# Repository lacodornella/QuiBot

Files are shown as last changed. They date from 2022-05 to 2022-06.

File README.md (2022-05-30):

# QuiBot

QuiBot is a robot to experiment basic sequential programming for children. No computer is needed as it can be programmed by using painted wooden blocks, where each color represents a different action. The robot has a backpack that can contain up to 12 blocks that execute as soon as they're consumed.

QuiBot Image

## Project folders

The project uses the following folders:
 - [3D Design](./3D_design/): 3D assembly process, BOM and printing files
 - [ESP-32 Arduino program](./QuiBot/): C++ Arduino program
 - [Kicad PCB project](./PCB_QuiBot/): Kicad PCB project
 - [Images](./Images/): Used to store some project images

## Development

This robot has been conceived and developed by Aleix Badia and [Pau Lafoz](https://www.github.com/pau-lafoz) from La Codornella under the UPC project "Qui-Bot H2O", led by Marta Tarrés and Toni Dorado, and funded by FECYT.

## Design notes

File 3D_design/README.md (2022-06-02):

# 3D Design

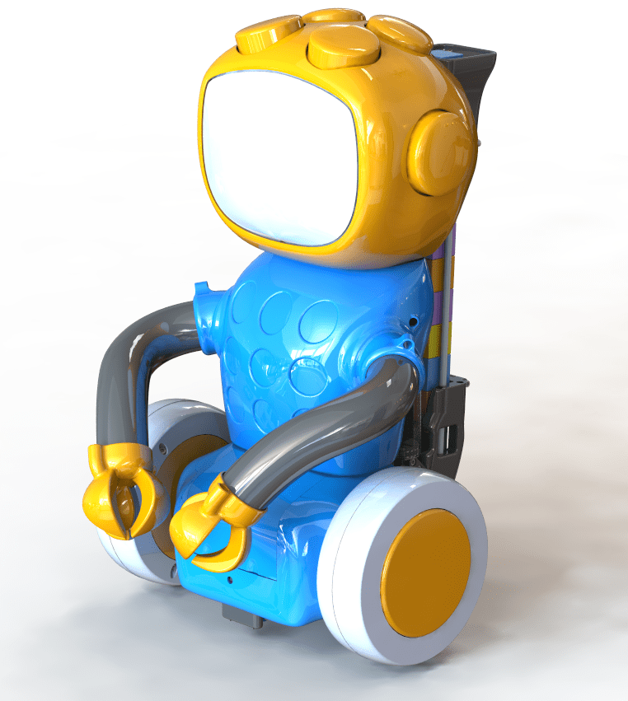
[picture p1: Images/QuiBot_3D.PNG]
QuiBot 3D


## Printing process
The list and details of all printable parts in the project can be found on [3D_Parts_list](./3D_parts_list.pdf) file.

Other considerations:
 - 5 printing configurations are used in the project.
 - All the printings can be done with standard 20 cm cube volume FDM printer.
 - The printing positions are shown in the folder "3D printing positioning captions". 

## Bill of materials
Detailed on the [BOM](./BOM.pdf) and [BOM Screws](./BOM_Screws.pdf) files. 

## Assembly process
The assembly process can be done using the schematic [QuiBot_drawings.pdf](./QuiBot_drawings.PDF) and opening the [Qui-bot.FCStd](./Qui-bot.FCStd) document with FreeCad for further details. 

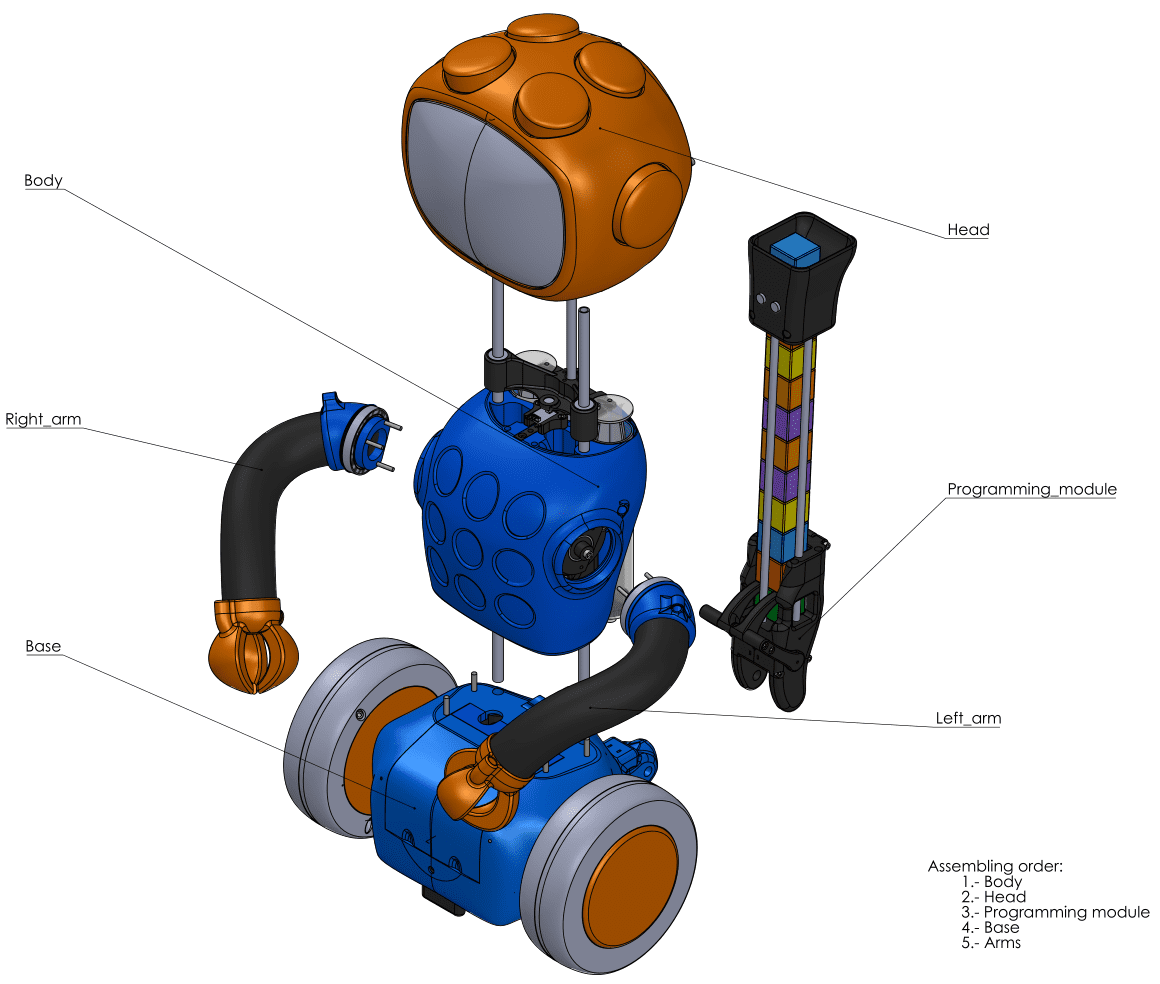
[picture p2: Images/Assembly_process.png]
Assembly process


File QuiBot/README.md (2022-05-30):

# QuiBot Arduino program

## Installation

The ESP32 controller can be programmed using Arduino IDE. The following libraries are required:
 - [FastLed](https://github.com/FastLED/FastLED)
 - [Adafruit_VL53L0X](https://github.com/adafruit/Adafruit_VL53L0X)
 - [TCS34725](https://github.com/hideakitai/TCS34725)
 - [AccelStepper](https://github.com/waspinator/AccelStepper)

 ## Hardware

The controller used is an ESP32 that controls the following devices:
 - Motion:
    - Wheels: 2x NEMA 17 Steppers with planetary reductor
    - Arms: 2x NEMA 17 Steppers with timing belt reduction
    - Syringe: NEMA 17 Stepper with endless screw
    - Block ejection: 5V Servomotor
 - Sensors:
    - Color sensor: TCS34725
    - Laser distance sensor: VL53L0X
    - Line follower: 2x TCRT5000
    - Arm endstops: 2x Hall effect sensor
    - Syringe endstop: Hall effect sensor
 - Eyes:
    - 2x 8x8 Adressable RGB Led matrix

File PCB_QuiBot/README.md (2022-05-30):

# QuiBot Kicad Project

## 3D View
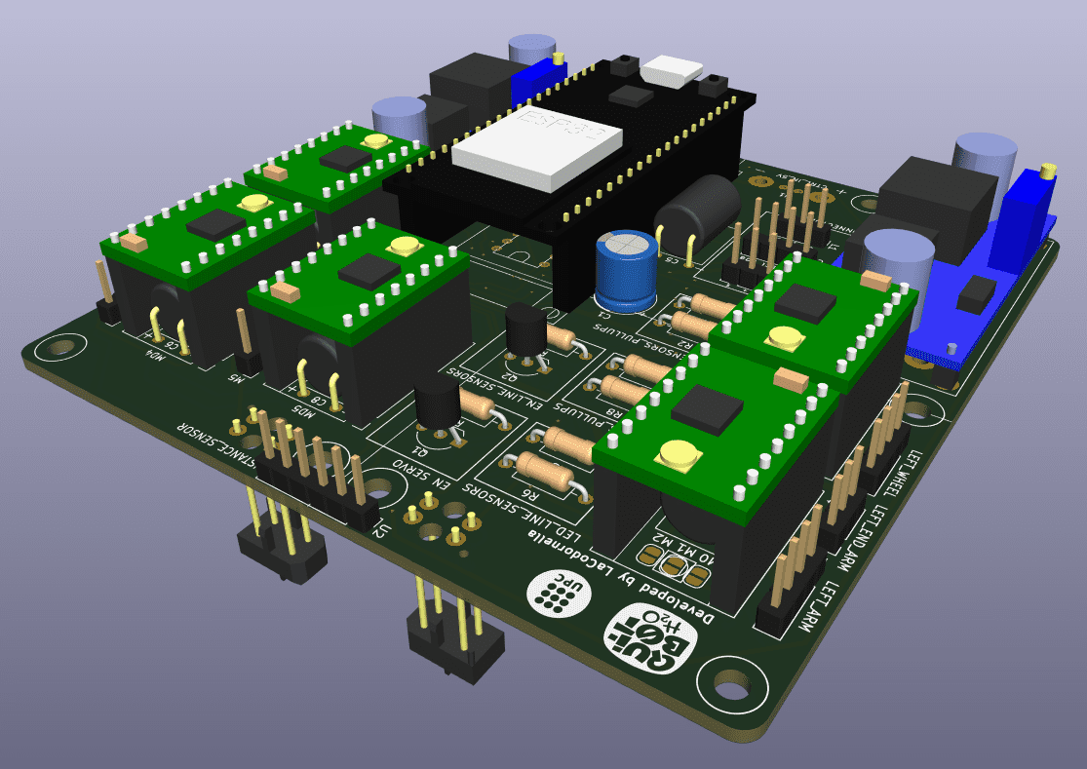
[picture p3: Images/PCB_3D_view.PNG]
PCB QuiBot 3D view


## Layout
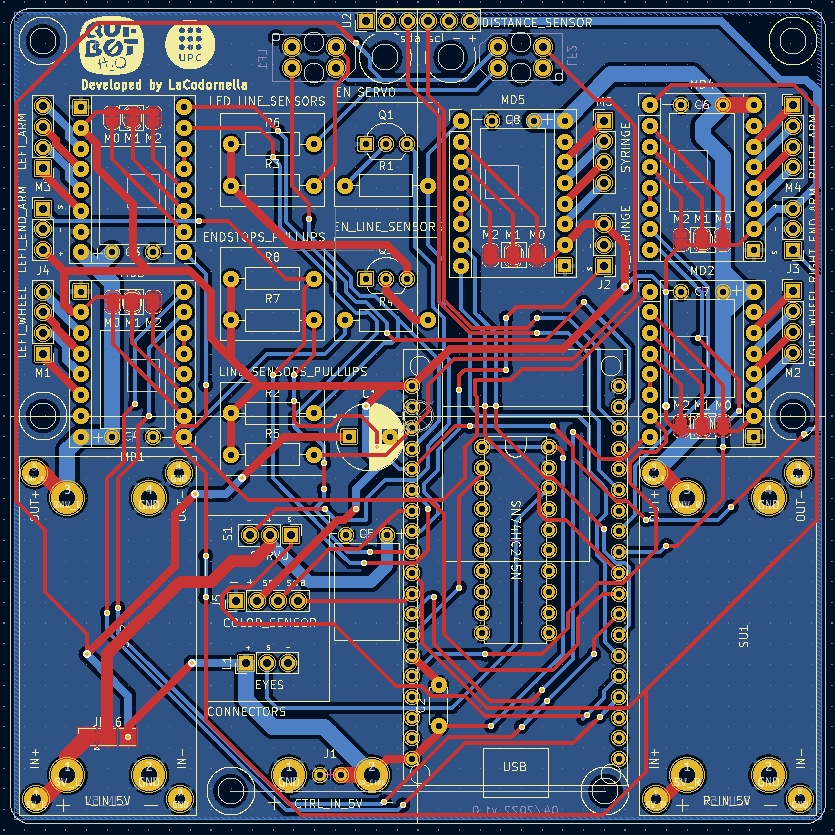
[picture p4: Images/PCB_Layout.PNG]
PCB QuiBot Layout


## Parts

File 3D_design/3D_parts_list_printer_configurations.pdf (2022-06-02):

| | QuiBot_1 | QuiBot_2 | QuiBot_3 | QuiBot_4 | QuiBot_5
Quality | Layer Height | 0.2 | 0.2 | 0.15 | 0.2 | 0.15
| Initial Layer Height | 0.15 | 0.15 | 0.15 | 0.15 | 0.15
Walls | Wall thikness | 0.8 | 0.8 | 0.8 | 2.0 | 2.0
Top/Bottom | Top/bottom pattern | Lines | Lines | Lines | Lines | Lines
| Bottom pattern initial layer | Concentric | Lines | Lines | Lines | Lines
Infill | Infill density | 10% | 25% | 15% | 15% | 40%
Material | Printing temperature | 200ºC | 200ºC | 200ºC | 200ºC | 200ºC
| Speed | 60 mm/s | 40 mm/s | 50 mm/s | 50 mm/s | 50 mm/s
Support | Generate support
| Support Overhang Angle | | 84º | 84º | 84º | 84º

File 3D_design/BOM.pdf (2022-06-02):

Module | Name in design | Component | Utilitzation | Price | Percent total price Shop | Comments | Link

Moviment

Nema17_5.18_reduction | Stepper amb reductor R | Moviment de la roda dreta del robot | 45,46 € | 10,82% | AliExpress | Compra pak de 4 a través d'aliexpress | https://es.aliexpress.com/item/4000222067282.html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
Nema17_5.18_reduction | Stepper amb reductor L | Moviment de la roda esquerra del robot | 45,46 € | 10,82% | AliExpress | Compra pak de 4 a través d'aliexpress | https://es.aliexpress.com/item/4000222067282.html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
Pololu_A4988 | Controlador A4988 DRV8825 | Controlador roda dreta | 2,20 € | 0,52% | Amazon | Compra pack de 5 a Amazon | https://www.amazon.es/UKCOCO-Reprap-Stepper-disipador-impresora/dp/B07BMR39GQ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
Pololu_A4988 | Controlador A4988 DRV8825 | Controlador roda esquerra | 2,20 € | 0,52% | Amazon | Compra pack de 5 a Amazon | https://www.amazon.es/UKCOCO-Reprap-Stepper-disipador-impresora/dp/B07BMR39GQ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
TCRT_5000_Line_follower | Sensor detector de línia dret | Detecció de la línia dreta | 0,49 € | 0,12% | Amazon | Compra pack de 10 a Amazon | https://www.amazon.es/gp/product/B08CSRNCMG/ref=ox_sc_act_title_1?smid=A1A94E00UJ9A5S&psc=1
TCRT_5000_Line_follower | Sensor detector de línia esquerra | Detecció de la línia esquerra | 0,49 € | 0,12% | Amazon | Tub de 5 a RS | https://www.amazon.es/gp/product/B08CSRNCMG/ref=ox_sc_act_title_1?smid=A1A94E00UJ9A5S&psc=1
CJVL53LOXV2_IR_distanse_sensor Sensor de distància GY-VL53L0XV2 | Detecció del pot de plàstic | 4,75 € | 1,13% | Amazon | Compra pack de 3 a Amazon | https://www.amazon.es/Haudboin-VL53L0X-Sensor-distancia-GY-VL53L0XV2/dp/B09QCJM193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
DC-DC_XL6009E1 | Step up | Elevació 5V poqer bank a 12V pels steppers | 2,41 € | 0,57% | Amazon | Compra pack de 5 a Amazon | https://www.amazon.es/TECNOIOT-XL6009-Booster-Adjustable-Step-up/dp/B07HB3GMZD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

Braços

Syringe | 2 Xeringues amb tub | Xeringues per xuclar el líquid | 11,15 € | 2,66% | Amazon | Compra pack de 2 a Amazon | https://www.amazon.es/dp/B081RL7BMH/?coliid=I3OZAKCWK8IAB6&colid=2GDHV7MAEUG1F&psc=1&ref_=lv_ov_lig_dp_it
Worm_gear_bar | Barra roscada lineal | Actuador per moure l'èmbol de les xeringues | 6,19 € | 1,47% | Amazon | Compra individual a Amazon | https://www.amazon.es/SIENOC-Impresora-Varilla-Carril-lineal/dp/B07LDZY8RY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
Nema17 | Stepper nema 17 Xeringa | Motor xeringa | 7,07 € | 1,68% | Amazon | Compra pack de 3 a Amazon | https://www.amazon.es/dp/B092ZD2WMV/ref=twister_B09BZHBBB5?_encoding=UTF8&psc=1
Nema17 | Stepper nema 17 R | Motor del braç dret | 7,07 € | 1,68% | Amazon | Compra pack de 3 a Amazon | https://www.amazon.es/dp/B092ZD2WMV/ref=twister_B09BZHBBB5?_encoding=UTF8&psc=1
Nema17 | Stepper nema 17 L | Motor del braç esquerra | 7,07 € | 1,68% | Amazon | Compra pack de 3 a Amazon | https://www.amazon.es/dp/B092ZD2WMV/ref=twister_B09BZHBBB5?_encoding=UTF8&psc=1
Pololu_A4988 | Controlador A4988 DRV8825 | Controlador braç dret | 2,20 € | 0,52% | Amazon | Compra pack de 5 a Amazon | https://www.amazon.es/UKCOCO-Reprap-Stepper-disipador-impresora/dp/B07BMR39GQ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
Pololu_A4988 | Controlador A4988 DRV8825 | Controlador braç esquerra | 2,20 € | 0,52% | Amazon | Compra pack de 5 a Amazon | https://www.amazon.es/UKCOCO-Reprap-Stepper-disipador-impresora/dp/B07BMR39GQ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
Pololu_A4988 | Controlador A4988 DRV8825 | Controlador motor xeringa | 2,20 € | 0,52% | Amazon | Compra pack de 5 a Amazon | https://www.amazon.es/UKCOCO-Reprap-Stepper-disipador-impresora/dp/B07BMR39GQ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
Hall_sensor | Fi de cursa dels braços | Detectar el final del moviment de cada un dels braços | 3,71 € | 0,88% | Amazon | Compra pack de 6 a Amazon | https://www.amazon.es/GTIWUNG-interruptor-Interruptor-Compatible-Impresora/dp/B07VWRS24K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
DC-DC_XL6009E1 | Step up | Elevació 5V power bank a 12V pels steppers | 4,81 € | 1,15% | Amazon | Compra pack de 5 a Amazon | https://www.amazon.es/TECNOIOT-XL6009-Booster-Adjustable-Step-up/dp/B07HB3GMZD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
| Corretges 200 mm reducció braços | Reduir el parell necessari per aixecar els braços guanyant precissió a la punta | 2,18 € | 0,52% | Amazon | Compra pack de 10 a Amazon | https://www.amazon.es/3Dman-GT2-distribuci%C3%B3n-impresora-unidades/dp/B07V6N32B1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
Bearing_52_40_7 | 2 x Rodaments 6808ZZ - 40 mm x 52 mm x 7 mm | Guiar exteriorment el moviments dels braços | 11,09 € | 2,64% | Amazon | Compra pack de 4 a Amazon | https://www.amazon.es/gp/product/B081JT8WJY/ref=ppx_yo_dt_b_asin_title_o06_s00?ie=UTF8&psc=1
608_2RS bearing | 4 x Rodaments 604-609 WX2RS | Guiar interiorment el moviments dels braços | 6,62 € | 1,58% | Amazon | Compra pack de 10 a Amazon | https://www.amazon.es/gp/product/B07JJ526NX/ref=ppx_yo_dt_b_asin_title_o00_s00?ie=UTF8&th=1
Lineal_bearing | 2 x Rodaments lineals de 8mm de diàmetre interior Guiar el moviment de les xeringues | 1,38 € | 0,33% | Amazon | Compra pack de 12 a Amazon | https://www.amazon.es/QWORK-LM8UU-Rodamientos-lineales-impresora/dp/B086W1LMMZ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
8x2.5_Magnet | 9 x Imants de neodimi N52. Discs de 8x3 mm | Finals de cursa dels braços, les xeringues i unió del bloc programador | 3,57 € | 0,85% | Amazon | Compra pack de 25 a Amazon | https://www.amazon.es/gp/product/B00Z7YVU8A/ref=ppx_yo_dt_b_search_asin_title?ie=UTF8&psc=1
| 2 x molles 35mm x 7mm x 0,5mm | Contrapes braços. | 0,09 € | 0,02% | Amazon | Compra pack a Amazon | https://www.amazon.es/gp/product/B01KG024CU/ref=ppx_yo_dt_b_search_asin_title?ie=UTF8&psc=1

Estètica

8x8_LED_matrix | Matriu LED 8x8 ull dret | matrius LED per fer d'ull dret | 17,26 € | 4,11% | Amazon | Compra individual a Amazon | https://www.amazon.es/BTF-LIGHTING-0-24ft0-24ft-Programmed-Individually-Addressable/dp/B01DC0IMRW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
8x8_LED_matrix | Matriu LED 8x8 ull esquerra | matrius LED per fer d'ull esquerra | 17,26 € | 4,11% | Amazon | Compra individual a Amazon | https://www.amazon.es/BTF-LIGHTING-0-24ft0-24ft-Programmed-Individually-Addressable/dp/B01DC0IMRW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

Bloc
programador
TCS34725_RGB_sensor | TCS34725 RGB Color Sensor | Llegir el color dels blocs de fusta | 4,42 € | 1,05% | Amazon | Compra pack de 5 a Amazon | https://www.amazon.es/dp/B07YXDZVJN/?coliid=IXUG4P6WHKAOW&colid=2GDHV7MAEUG1F&psc=1&ref_=lv_ov_lig_dp_it
SG90 - Micro Servo 9g | Servo Motor SG90 | Expulsar els blocs un cop llegits | 2,64 € | 0,63% | Amazon | Compra pack de 5 a Amazon | https://www.amazon.es/Micro-Helicopter-Airplane-Controls-LKY66-UK-5/dp/B07236KYVC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

Controlador

ESP32_DEVKIT_AZD | ESP32 | Microcontrolador | 6,61 € | 1,57% | Amazon | Compra pack de 5 a Amazon | https://www.amazon.es/AZDelivery-NodeMCU-ESP-WROOM-32-Tablero-Desarrollo/dp/B074RG86SR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
Power_bank | Power bank 10000 mAh LEFT | Power bank 10000 mAh costat dret | 12,63 € | 3,01% | Amazon | Compra individual a Amazon | https://www.amazon.es/BABAKA-10000mAh-Cargador-Port%C3%A1til-Tecnolog%C3%ADa/dp/B08H89HP33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
Power_bank | Power bank 10000 mAh RIGHT | Power bank 10000 mAh costat esquerre | 12,63 € | 3,01% | Amazon | Compra individual a Amazon | https://www.amazon.es/BABAKA-10000mAh-Cargador-Port%C3%A1til-Tecnolog%C3%ADa/dp/B08H89HP33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
Power_bank | Power bank 10000 mAh controlador i resta | Power bank 10000 mAh controlador i resta | 12,63 € | 3,01% | Amazon | Compra individual a Amazon | https://www.amazon.es/BABAKA-10000mAh-Cargador-Port%C3%A1til-Tecnolog%C3%ADa/dp/B08H89HP33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
PCB_QuiBot | PCB | | 25,00 € | 5,95% | Fabricació a ELECROW
| Electrònica soldada a la PCB | | 15,00 € | 3,57% | Botiga genèrica d'electrònica

Altres

Strucutural_vertical_bar | materials constructius (fusta i tubs alumini) | | 40,00 € | 9,52% | Fes més bricolatge
| Impressió 3D | 2,1 Kg de plàstic contats a 20€ el Kg | 41,86 € | 9,97% | | | https://www.amazon.es/gp/product/B08LSF322C/ref=ppx_yo_dt_b_asin_title_o08_s00?ie=UTF8&th=1
| Cargoleria *Detallat al full cargoleria | | 30,00 € | 7,14% | Botiga genèrica de cargoleria
Total: | 419,96 €

Opcionals

Lona decorat | 60,00 € | https://www.ecoimpresion.es/lonas/pvc.html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
Pots de plàstic | 20,00 €
Total: | 80,00 €
Total + opcionals: | 499,96 €

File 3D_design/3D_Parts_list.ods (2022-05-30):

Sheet: 3D printed parts
 |  | 252:25:00 | 2093
 | Name | Printing time | Plastic (g) | Material | Configuration
1 | Arms_motors_support_bottom | 2:49:00 | 24 | PLA negre | QuiBot_2
1 | Arms_motors_support_top | 3:11:00 | 27 | PLA negre | QuiBot_2
1 | Ball_support | 2:13:00 | 18 | PLA blau | QuiBot_3
1 | Ball_support_inferior | 0:23:00 | 3 | PLA blau | QuiBot_3
1 | Batteries_lid | 3:15:00 | 29 | PLA blau | QuiBot_3
1 | Batteries_support | 8:03:00 | 82 | PLA negre | QuiBot_4
1 | Big_pulley | 2:17:00 | 21 | PLA negre | QuiBot_2
1 | Big_pulley_mirror | 2:17:00 | 21 | PLA negre | QuiBot_2
1 | Block_insert | 5:35:00 | 42 | PLA negre | QuiBot_3
1 | Body | 41:46:00 | 311 | PLA blau | QuiBot_3
1 | Elbow | 1:20:00 | 9 | PLA negre | QuiBot_3
1 | Elbow_mirror | 1:20:00 | 9 | PLA negre | QuiBot_3
1 | End_arm_bar | 0:05:00 | 1 | PLA negre | QuiBot_2
1 | End_arm_bar_mirror | 0:05:00 | 1 | PLA negre | QuiBot_2
1 | Extrude_head_1 | 1:59:00 | 16 | PLA taronja | QuiBot_3
1 | Extrude_head_1 | 1:59:00 | 16 | PLA taronja | QuiBot_3
1 | Extrude_head_2 | 1:58:00 | 24 | PLA taronja | QuiBot_3
1 | Extrude_head_2 | 1:58:00 | 24 | PLA taronja | QuiBot_3
1 | Extrude_head_3 | 1:40:00 | 19 | PLA taronja | QuiBot_3
1 | Extrude_head_3 | 1:40:00 | 19 | PLA taronja | QuiBot_3
1 | Eyes_support | 2:32:00 | 23 | PLA negre | QuiBot_1
1 | Head | 39:32:00 | 240 | PLA taronja | QuiBot_3
1 | Head_back | 7:45:00 | 71 | PLA taronja | QuiBot_3
1 | Interior_wheel | 5:58:00 | 83 | PLA taronja | QuiBot_1
1 | Interior_wheel_mirror | 5:58:00 | 83 | PLA taronja | QuiBot_1
1 | L_Motor_support | 21:16:00 | 147 | PLA blau | QuiBot_3
1 | Left_arm_spacing_part | 1:07:00 | 9 | PLA negre | QuiBot_3
1 | Left_arm_spacing_part_mirror | 1:07:00 | 9 | PLA negre | QuiBot_3
1 | Left_assembly_support | 3:57:00 | 33 | PLA negre | QuiBot_5
1 | Left_hall_support | 0:55:00 | 5 | PLA negre | QuiBot_3
1 | Left_hall_support_mirror | 0:55:00 | 5 | PLA negre | QuiBot_3
1 | Left_hand | 5:39:00 | 51 | PLA taronja | QuiBot_5
1 | Left_hand_mirror | 5:39:00 | 51 | PLA taronja | QuiBot_5
1 | Line_sensors_support | 0:49:00 | 5 | PLA negre | QuiBot_5
1 | Programming_block_magnets_union | 0:21:00 | 3 | PLA taronja | QuiBot_3
1 | Pusher_1 | 0:38:00 | 4 | PLA negre | QuiBot_5
1 | Pusher_1_mirror | 0:39:00 | 4 | PLA negre | QuiBot_5
1 | Pusher_2 | 0:32:00 | 4 | PLA negre | QuiBot_5
1 | Pusher_2_mirror | 0:32:00 | 4 | PLA negre | QuiBot_5
1 | Pusher_stopper | 0:20:00 | 3 | PLA negre | QuiBot_3
1 | Pusher_stopper_top | 1:28:00 | 11 | PLA negre | QuiBot_3
1 | R_Motor_support_mirror | 20:32:00 | 143 | PLA blau | QuiBot_3
1 | Right_assembly_support_mirror | 4:11:00 | 36 | PLA negre | QuiBot_5
1 | Shoulder | 2:26:00 | 19 | PLA negre | QuiBot_3
1 | Shoulder_mirror | 2:26:00 | 19 | PLA negre | QuiBot_3
1 | Syringe_hall_sensor_support | 0:22:00 | 2 | PLA negre | QuiBot_3
1 | Syringe_lifter | 3:07:00 | 19 | PLA negre | QuiBot_3
1 | Tension_screw_fixing_part | 0:46:00 | 5 | PLA negre | QuiBot_5
1 | Top_assembly_support | 1:28:00 | 11 | PLA negre | QuiBot_3
1 | Transparent_face | 8:27:00 | 81 | PLA transparent | QuiBot_4
1 | Union_and_cables_support | 1:00:00 | 8 | PLA negre | QuiBot_2
1 | Wheel | 7:04:00 | 93 | PLA gris | QuiBot_2
1 | Wheel_mirror | 7:04:00 | 93 | PLA gris | QuiBot_2

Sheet: Printer configurations
 |  | QuiBot_1 | QuiBot_2 | QuiBot_3 | QuiBot_4 | QuiBot_5
Quality | Layer Height | 0.2 | 0.2 | 0.15 | 0.2 | 0.15
 | Initial Layer Height | 0.15 | 0.15 | 0.15 | 0.15 | 0.15
Walls | Wall thikness | 0.8 | 0.8 | 0.8 | 2.0 | 2.0
Top/Bottom | Top/bottom pattern | Lines | Lines | Lines | Lines | Lines
 | Bottom pattern initial layer | Concentric | Lines | Lines | Lines | Lines
Infill | Infill density | 10% | 25% | 15% | 15% | 40%
Material | Printing temperature | 200ºC | 200ºC | 200ºC | 200ºC | 200ºC
 | Speed | 60 mm/s | 40 mm/s | 50 mm/s | 50 mm/s | 50 mm/s
Support | Generate support | 0 | 1 | 1 | 1 | 1
 | Support Overhang Angle |  | 84º | 84º | 84º | 84º

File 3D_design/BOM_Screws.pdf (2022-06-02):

Reference | Length | Qty
DIN912_M3 | 35 | 31
DIN912_M3 | 6 | 8
DIN912_M3 | 16 | 21
DIN912_M3 | 50 | 3
DIN912_M3 | 12 | 2
DIN912_M3 | 20 | 16
DIN912_M3 | 10 | 55
DIN912_M3 | 30 | 2
DIN912_M4 | 80 | 1
DIN912_M4 | 20 | 16

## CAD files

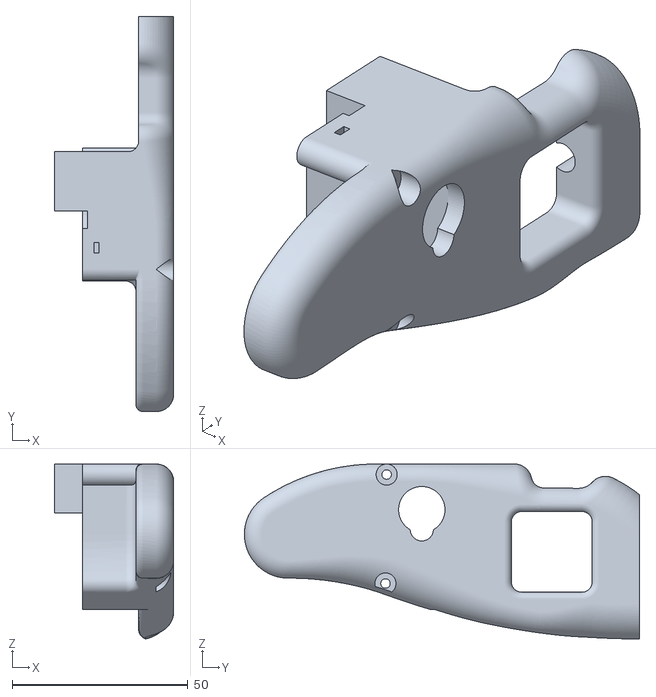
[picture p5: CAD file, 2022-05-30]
3D_design/STL/Left_assembly_support.STL
34.0 x 112.5 x 49.8

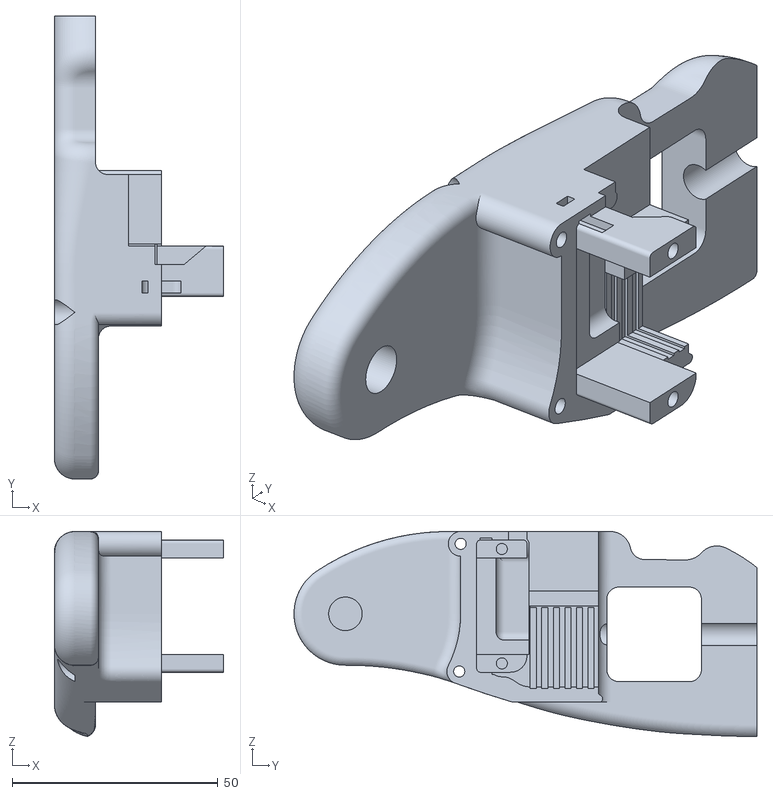
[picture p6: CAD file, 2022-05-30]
3D_design/STL/Right_assembly_support_mirror.STL
41.2 x 112.5 x 49.8

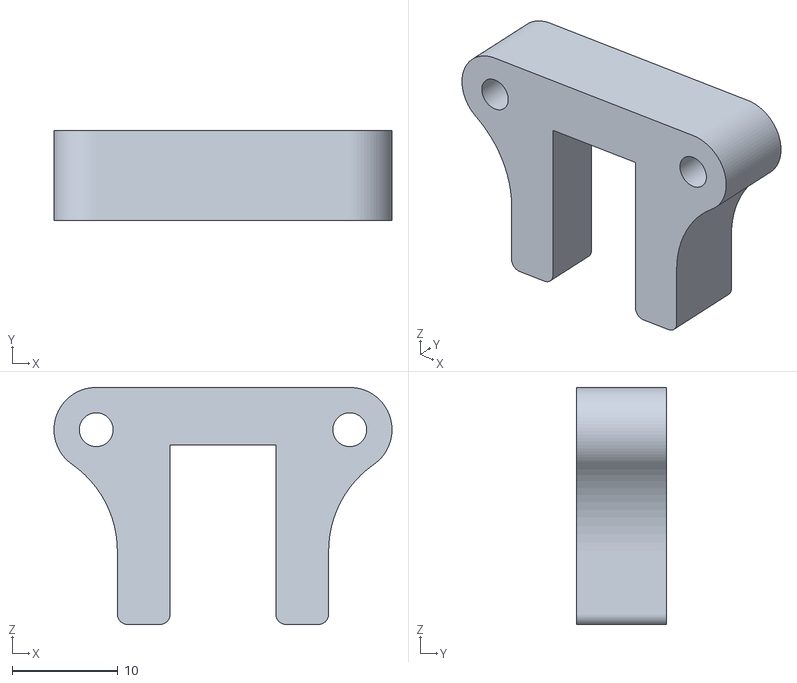
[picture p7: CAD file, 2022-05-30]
3D_design/STL/Syringe_hall_sensor_support.STL
32.0 x 8.50 x 22.5

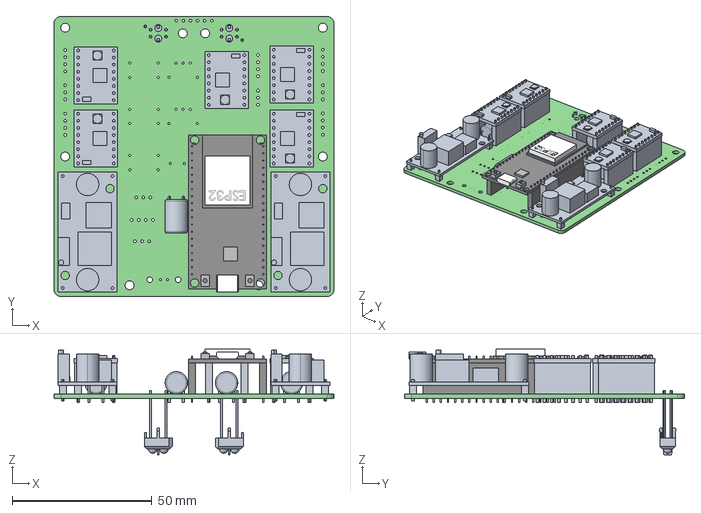
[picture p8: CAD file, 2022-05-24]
PCB_QuiBot/PCB_QuiBot.step
100.0 x 100.0 x 37.7 mm
_autosave-PCB_QuiBot PCB

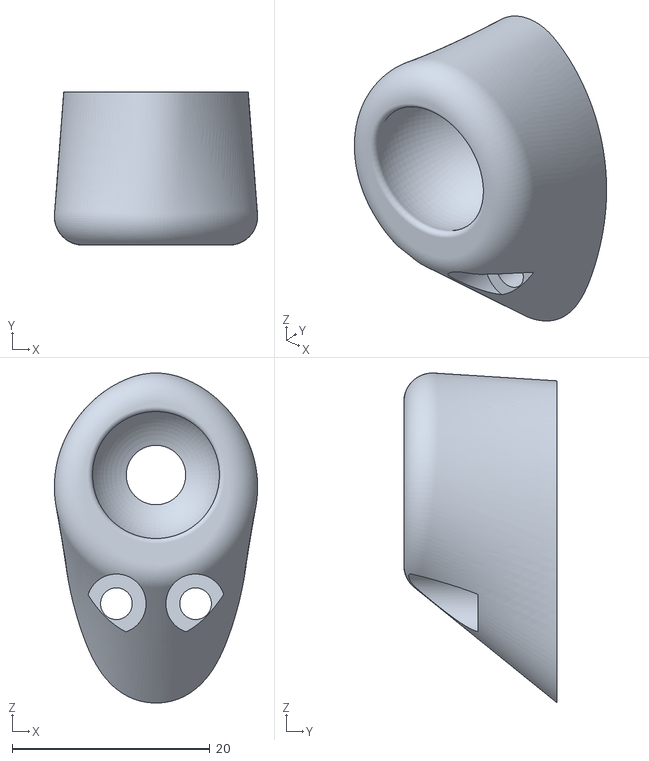
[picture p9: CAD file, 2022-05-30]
3D_design/STL/Ball_support_inferior.STL
20.5 x 15.5 x 33.3

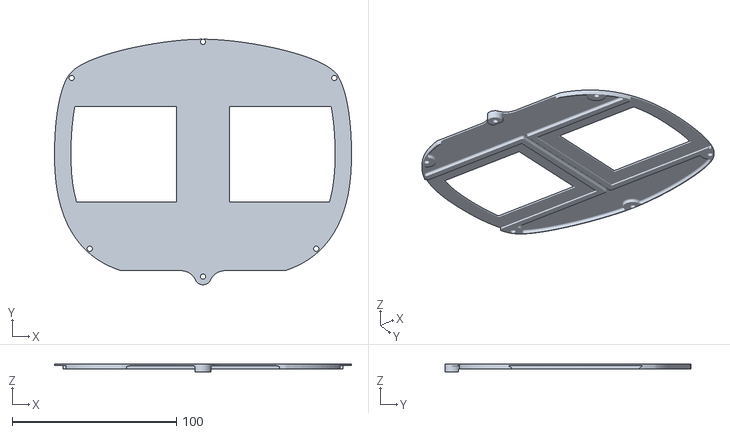
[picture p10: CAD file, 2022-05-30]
3D_design/STL/Eyes_support.STL
180.9 x 149.6 x 5.00

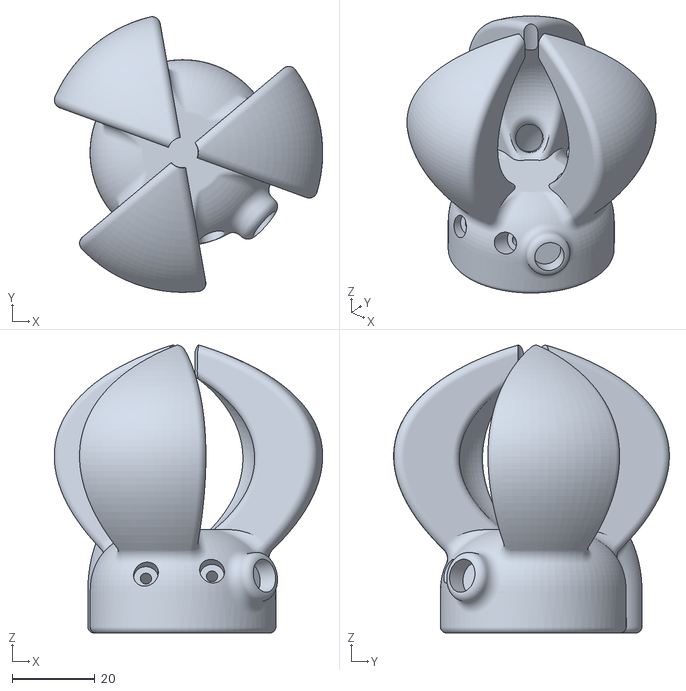
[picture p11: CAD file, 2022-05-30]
3D_design/STL/Left_hand_mirror.STL
65.0 x 66.7 x 69.7

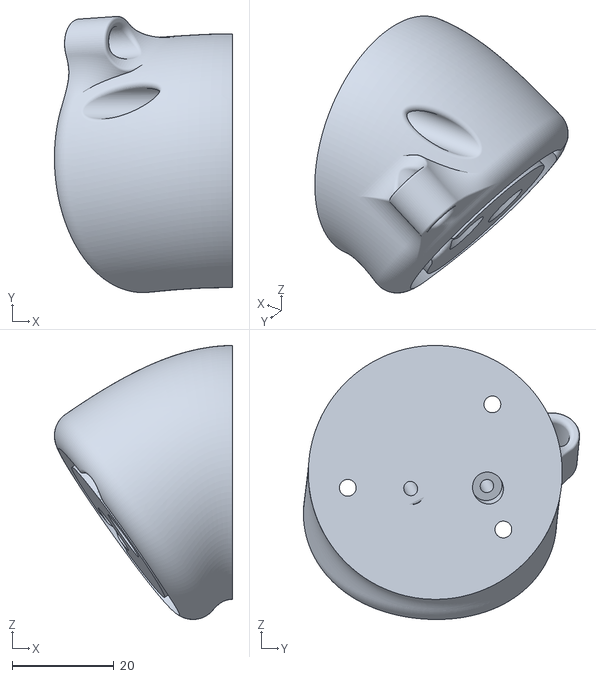
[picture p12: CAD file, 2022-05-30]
3D_design/STL/Shoulder.STL
35.1 x 54.4 x 54.0

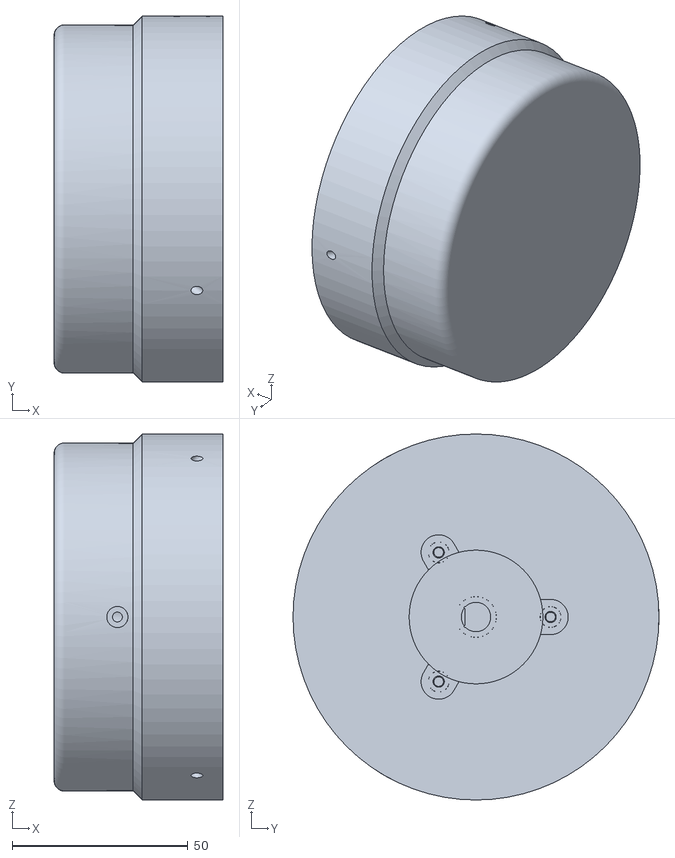
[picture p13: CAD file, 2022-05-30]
3D_design/STL/Interior_wheel.STL
48.0 x 104.0 x 104.0

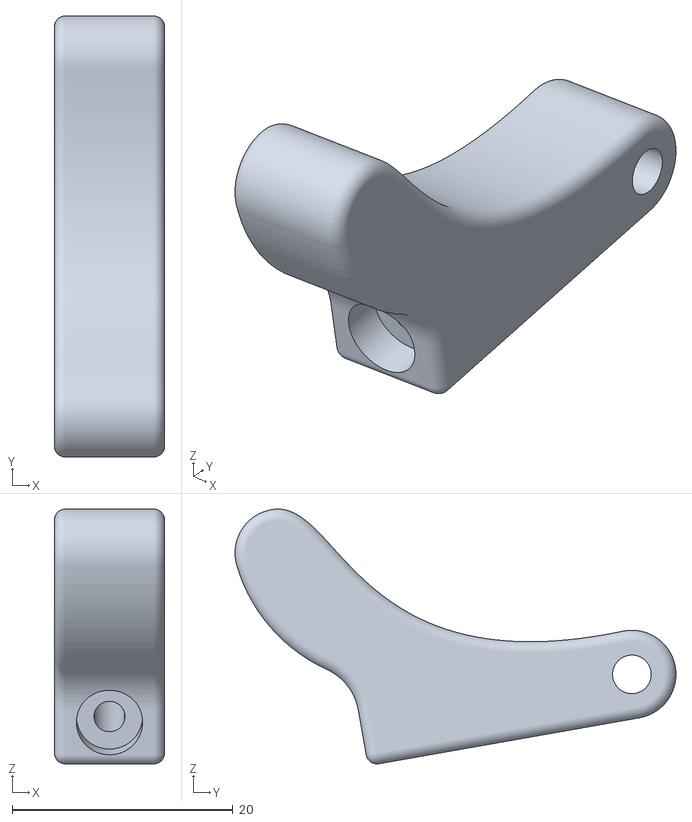
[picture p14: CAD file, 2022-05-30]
3D_design/STL/Pusher_stopper.STL
10.0 x 40.0 x 23.1

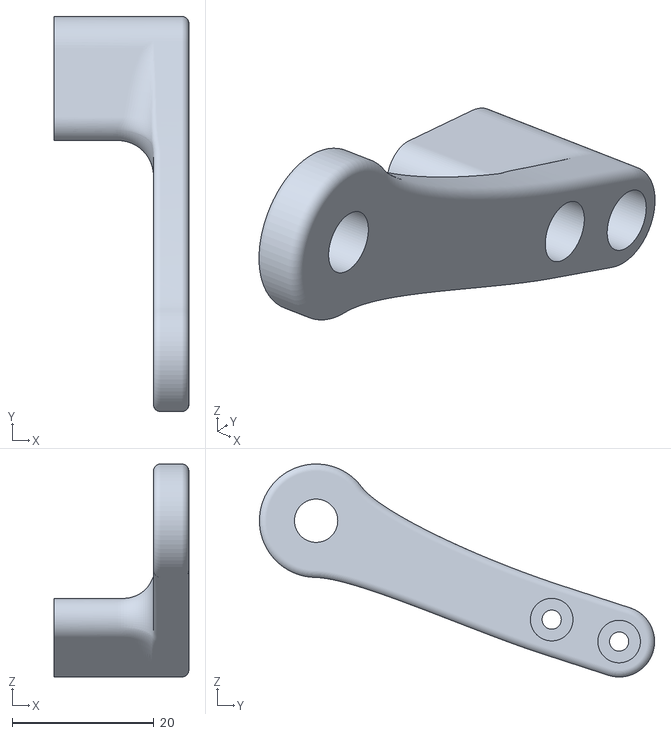
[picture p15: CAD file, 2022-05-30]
3D_design/STL/Pusher_1_mirror.STL
19.0 x 55.7 x 30.0

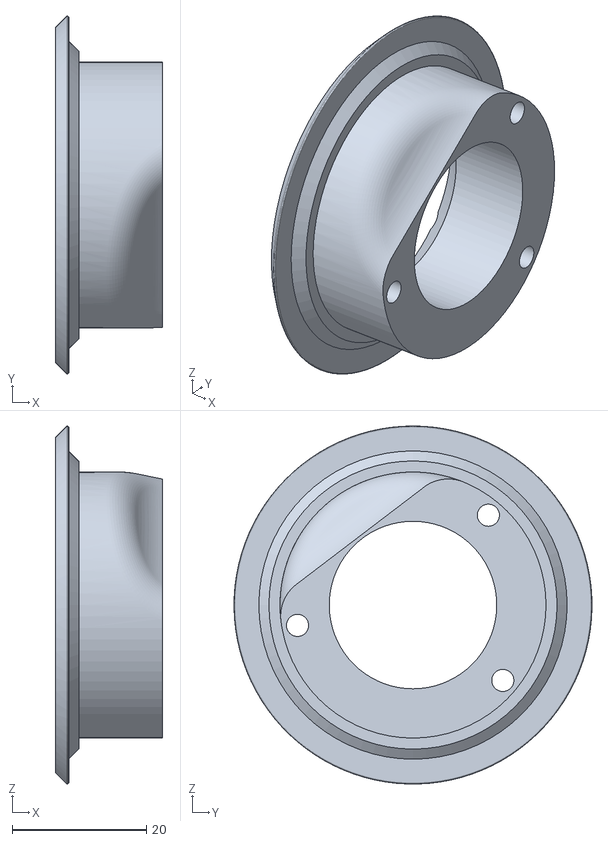
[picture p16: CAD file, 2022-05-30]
3D_design/STL/Left_arm_spacing_part.STL
16.0 x 53.4 x 53.4

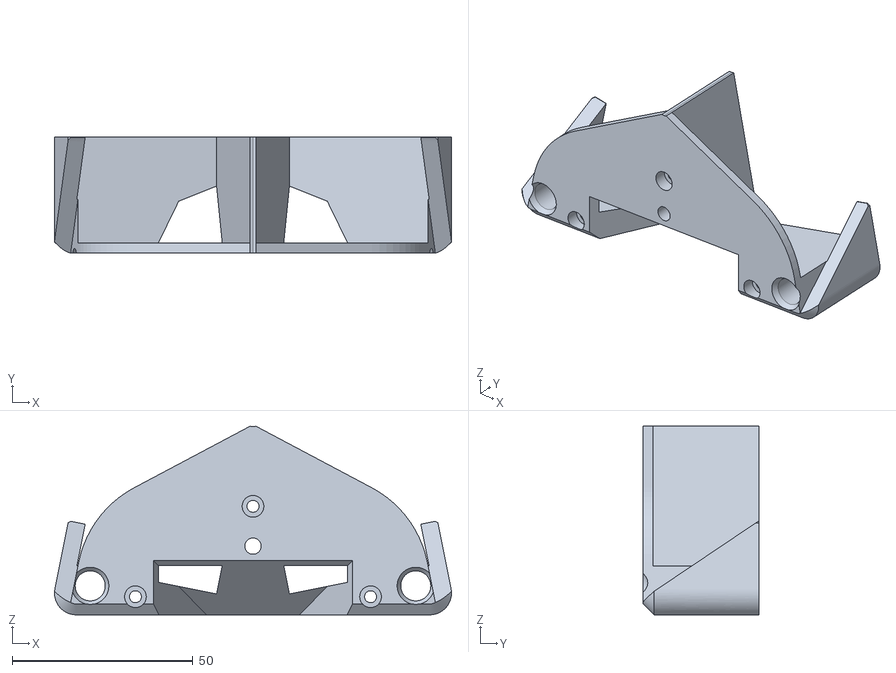
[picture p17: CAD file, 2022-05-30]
3D_design/STL/Arms_motors_support_top.STL
109.8 x 32.0 x 52.2

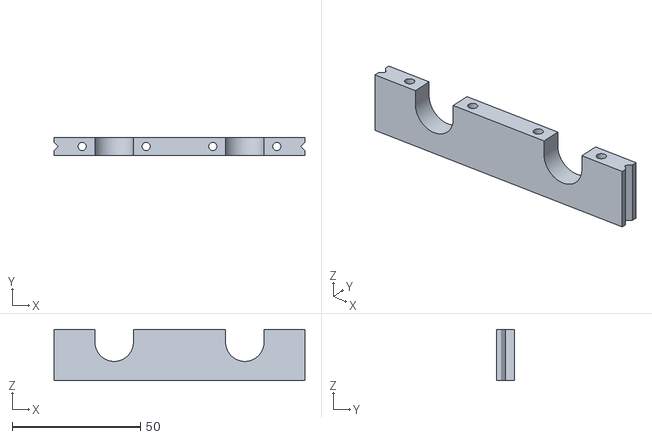
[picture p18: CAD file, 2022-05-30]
3D_design/STL/Union_and_cables_support.STL
98.0 x 7.00 x 20.0

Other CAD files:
3D_design/STL/End_arm_bar.STL
3D_design/STL/Wheel.STL
3D_design/STL/Wheel_mirror.STL
3D_design/STL/Arms_motors_support_bottom.STL
3D_design/STL/Ball_support.STL
3D_design/STL/Batteries_lid.STL
3D_design/STL/Batteries_support.STL
3D_design/STL/Big_pulley.STL
3D_design/STL/Big_pulley_mirror.STL
3D_design/STL/Block_insert.STL
3D_design/STL/Elbow.STL
3D_design/STL/Elbow_mirror.STL
3D_design/STL/Extrude_head_1.STL
3D_design/STL/Extrude_head_2.STL
3D_design/STL/Extrude_head_3.STL
3D_design/STL/Head_back.STL
3D_design/STL/Interior_wheel_mirror.STL
3D_design/STL/Left_arm_spacing_part_mirror.STL
3D_design/STL/Left_hall_support.STL
3D_design/STL/Left_hall_support_mirror.STL
3D_design/STL/Left_hand.STL
3D_design/STL/Line_sensors_support.STL
3D_design/STL/Programming_block_magnets_union.STL
3D_design/STL/Pusher_1.STL
3D_design/STL/Pusher_2.STL
3D_design/STL/Pusher_2_mirror.STL
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

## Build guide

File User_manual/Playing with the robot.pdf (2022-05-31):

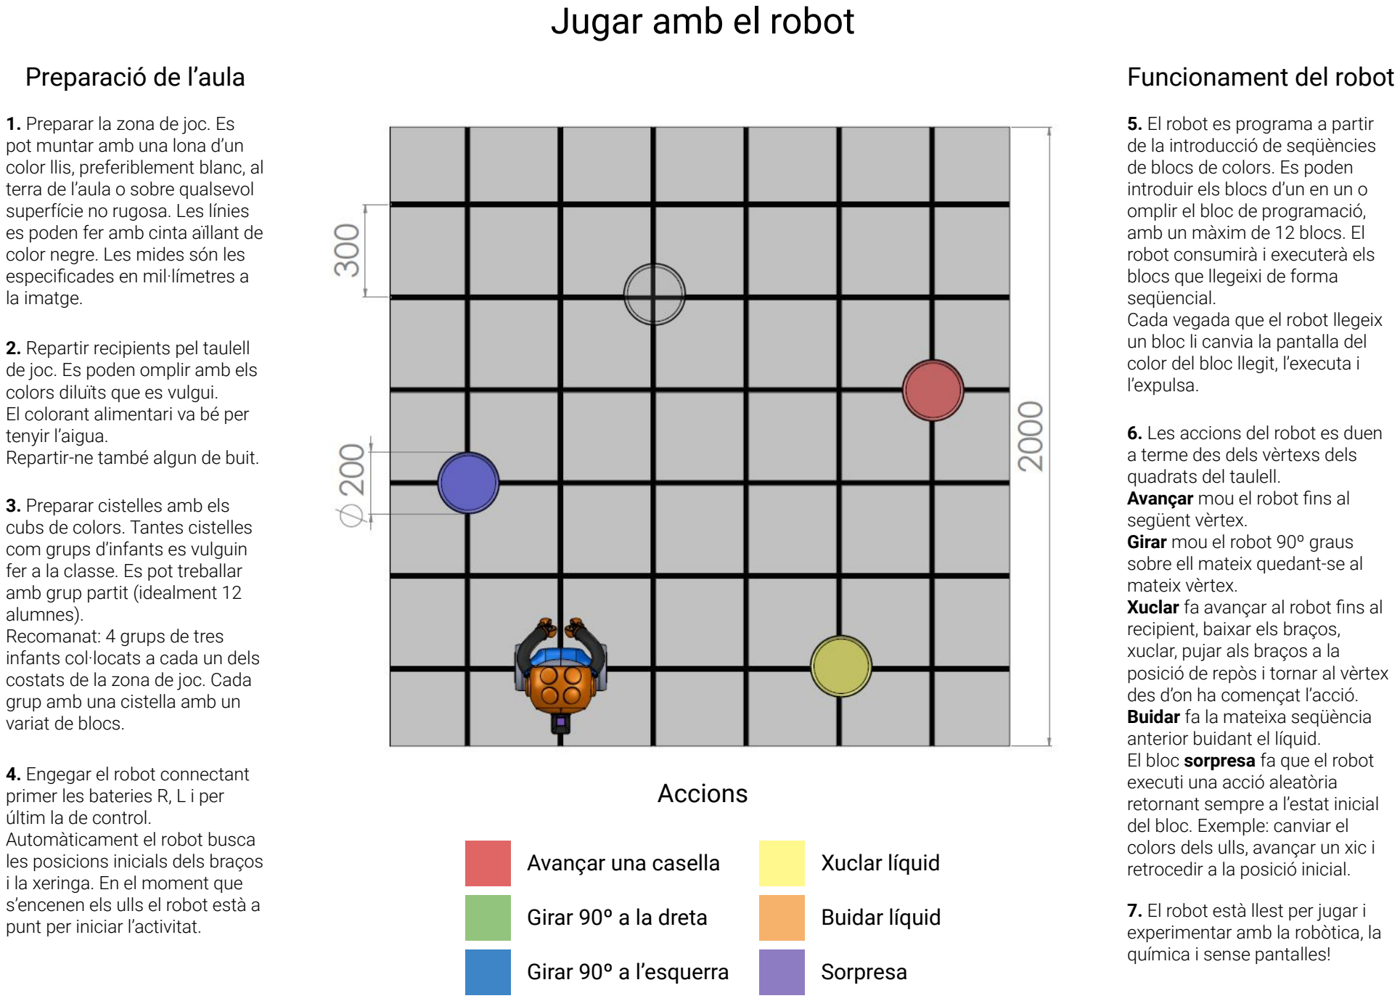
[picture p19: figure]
5. El robot es programa a partir de la introducció de seqüències de blocs de colors. Es poden introduir els blocs d’un en un o omplir el bloc de programació, amb un màxim de 12 blocs. El robot consumirà i executerà els blocs que llegeixi de forma seqüencial. Cada vegada que el robot llegeix un bloc li canvia la pantalla del color del bloc llegit, l’executa i l’expulsa.; 3. Preparar cistelles amb els cubs de colors. Tantes cistelles com grups d’infants es vulguin fer a la classe. Es pot treballar amb grup partit (idealment 12 alumnes). Recomanat: 4 grups de tres infants col·locats a cada un dels costats de la zona de joc. Cada grup amb una cistella amb un variat de blocs.; 2. Repartir recipients pel taulell de joc. Es poden omplir amb els colors diluïts que es vulgui. El colorant alimentari va bé per tenyir l’aigua. Repartir-ne també algun de buit.; Jugar amb el robot; 1. Preparar la zona de joc. Es pot muntar amb una lona d’un color llis, preferiblement blanc, al terra de l’aula o sobre qualsevol superfície no rugosa. Les línies es poden fer amb cinta aïllant de color negre. Les mides són les especificades en mil·límetres a la imatge.; 4. Engegar el robot connectant primer les bateries R, L i per últim la de control. Automàticament el robot busca les posicions inicials dels braços i la xeringa. En el moment que s’encenen els ulls el robot està a punt per iniciar l’activitat.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

Preparació de l’aula | Funcionament del robot

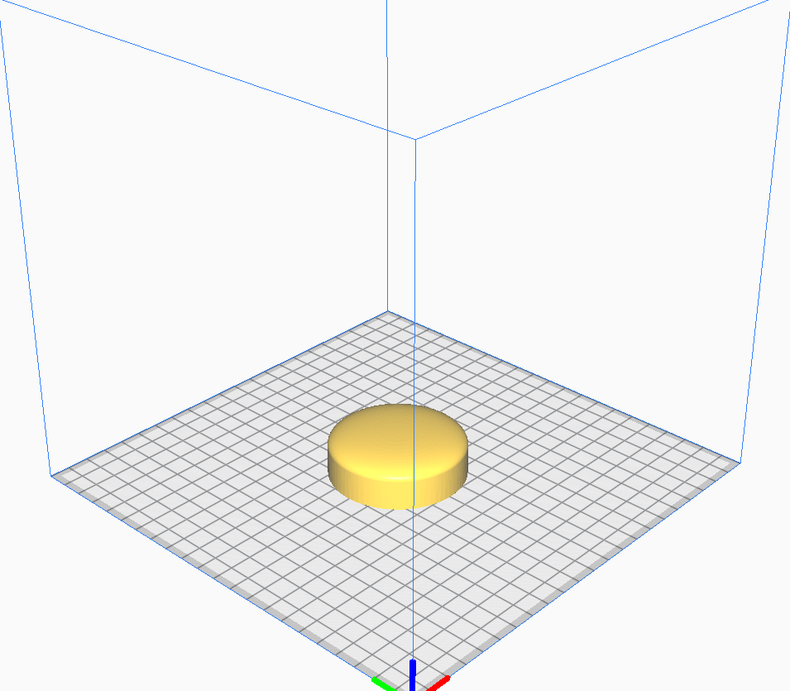
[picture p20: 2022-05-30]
3D_design/3D printing positioning captions/Extrude_head_1.PNG

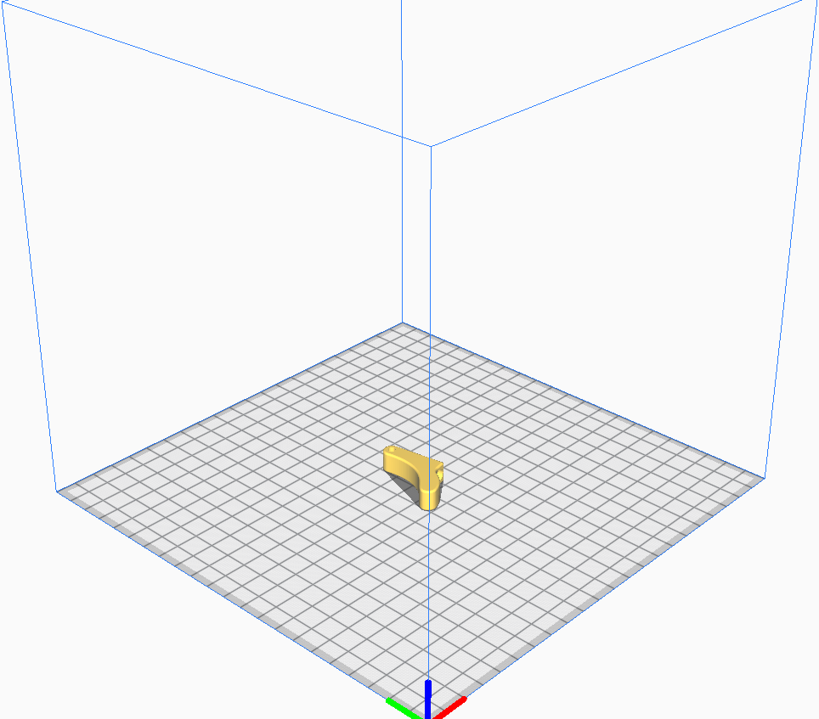
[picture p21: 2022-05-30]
3D_design/3D printing positioning captions/Pusher_stopper.PNG

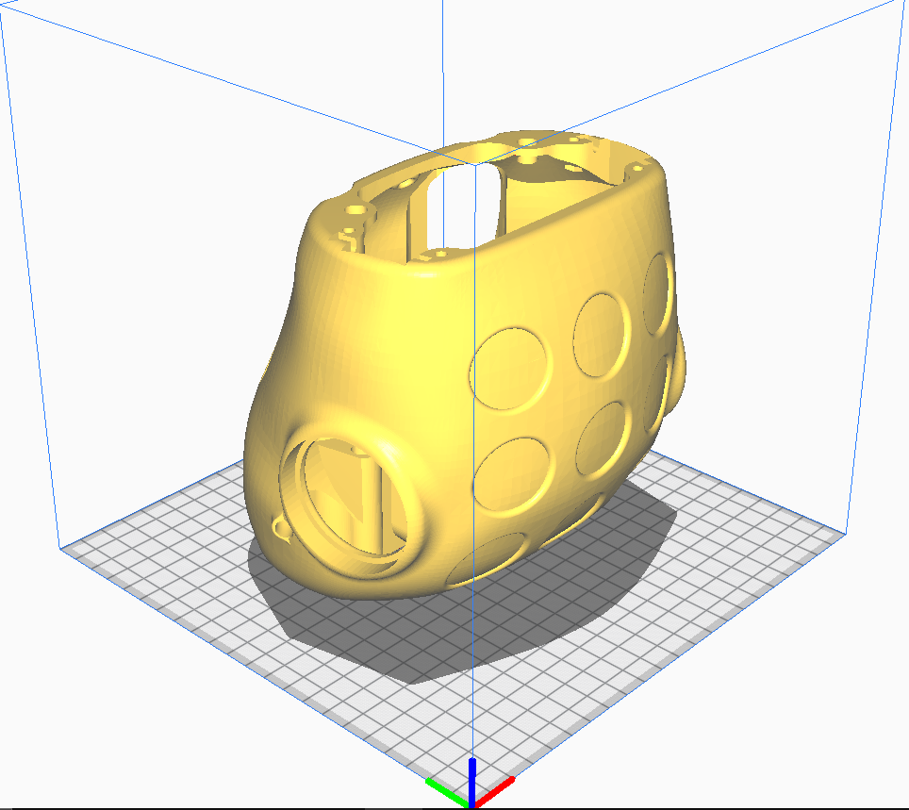
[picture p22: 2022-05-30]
3D_design/3D printing positioning captions/Body.PNG

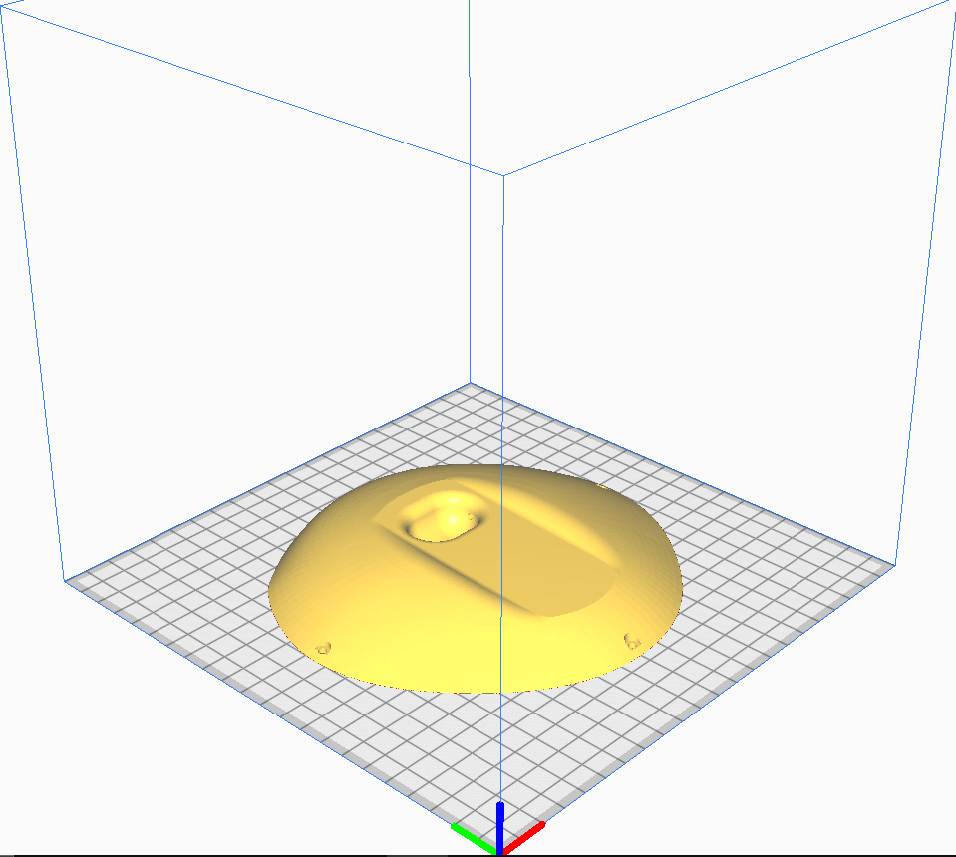
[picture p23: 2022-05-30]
3D_design/3D printing positioning captions/Head_back.PNG

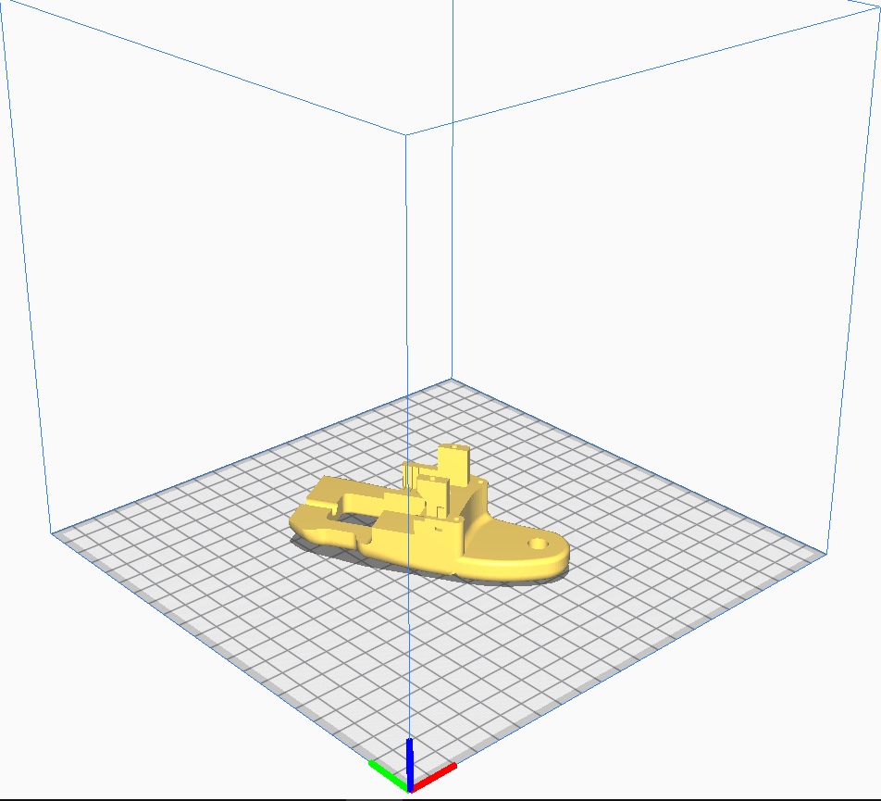
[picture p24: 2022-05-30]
3D_design/3D printing positioning captions/Right_assembly_support_mirror.PNG

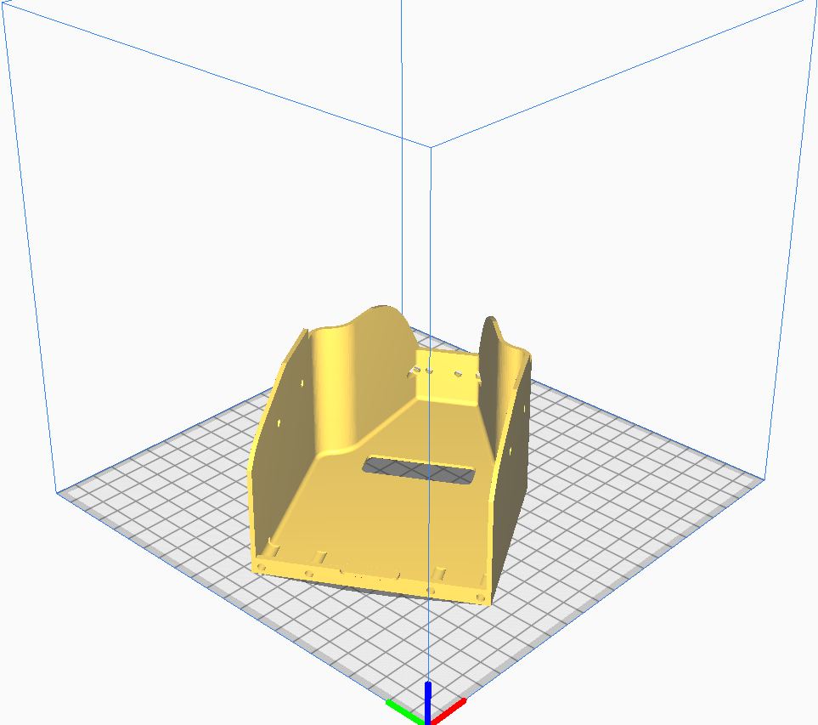
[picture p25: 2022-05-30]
3D_design/3D printing positioning captions/Batteries_support.PNG

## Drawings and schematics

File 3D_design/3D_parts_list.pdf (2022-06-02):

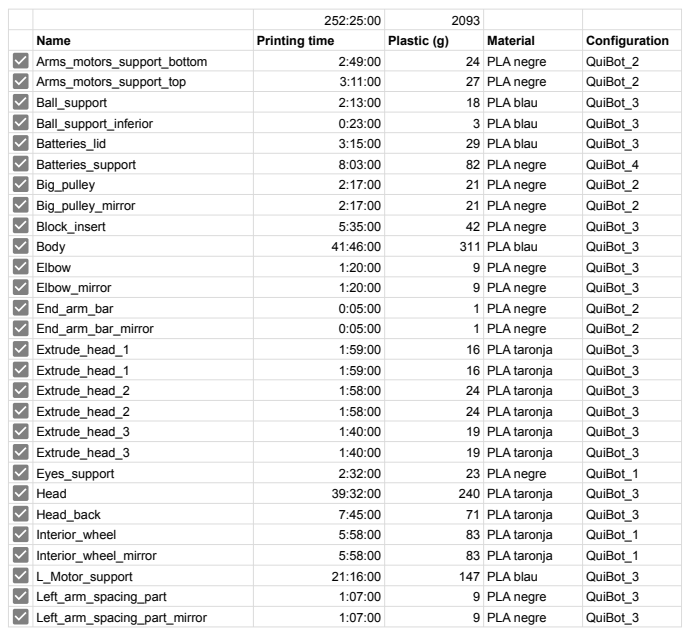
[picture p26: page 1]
Name; Printing time; Plastic (g); Material; Configuration; Arms_motors_support_bottom; 24 PLA negre; QuiBot_2; Arms_motors_support_top; 27 PLA negre; Ball_support; 18 PLA blau; QuiBot_3; Ball_support_inferior; 3 PLA blau; Batteries_lid; 29 PLA blau; Batteries_support; 82 PLA negre; QuiBot_4; Big_pulley; 21 PLA negre; Big_pulley_mirror; Block_insert; 42 PLA negre; Body; 311 PLA blau; Elbow; 9 PLA negre; Elbow_mirror; End_arm_bar; 1 PLA negre; End_arm_bar_mirror; Extrude_head_1; 16 PLA taronja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

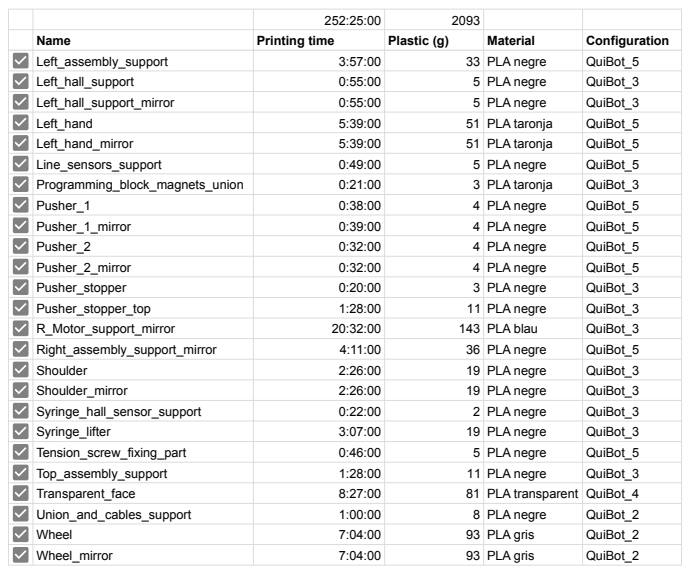
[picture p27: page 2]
Left_assembly_support; 33 PLA negre; QuiBot_5; Left_hall_support; 5 PLA negre; QuiBot_3; Left_hall_support_mirror; Left_hand; 51 PLA taronja; Left_hand_mirror; Line_sensors_support; Programming_block_magnets_union; 3 PLA taronja; Pusher_1; 4 PLA negre; Pusher_1_mirror; Pusher_2; Pusher_2_mirror; Pusher_stopper; 3 PLA negre; Pusher_stopper_top; 11 PLA negre; R_Motor_support_mirror; 143 PLA blau; Right_assembly_support_mirror; 36 PLA negre; Shoulder; 19 PLA negre; Shoulder_mirror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

Name | Printing time | Plastic (g) | Material | Configuration

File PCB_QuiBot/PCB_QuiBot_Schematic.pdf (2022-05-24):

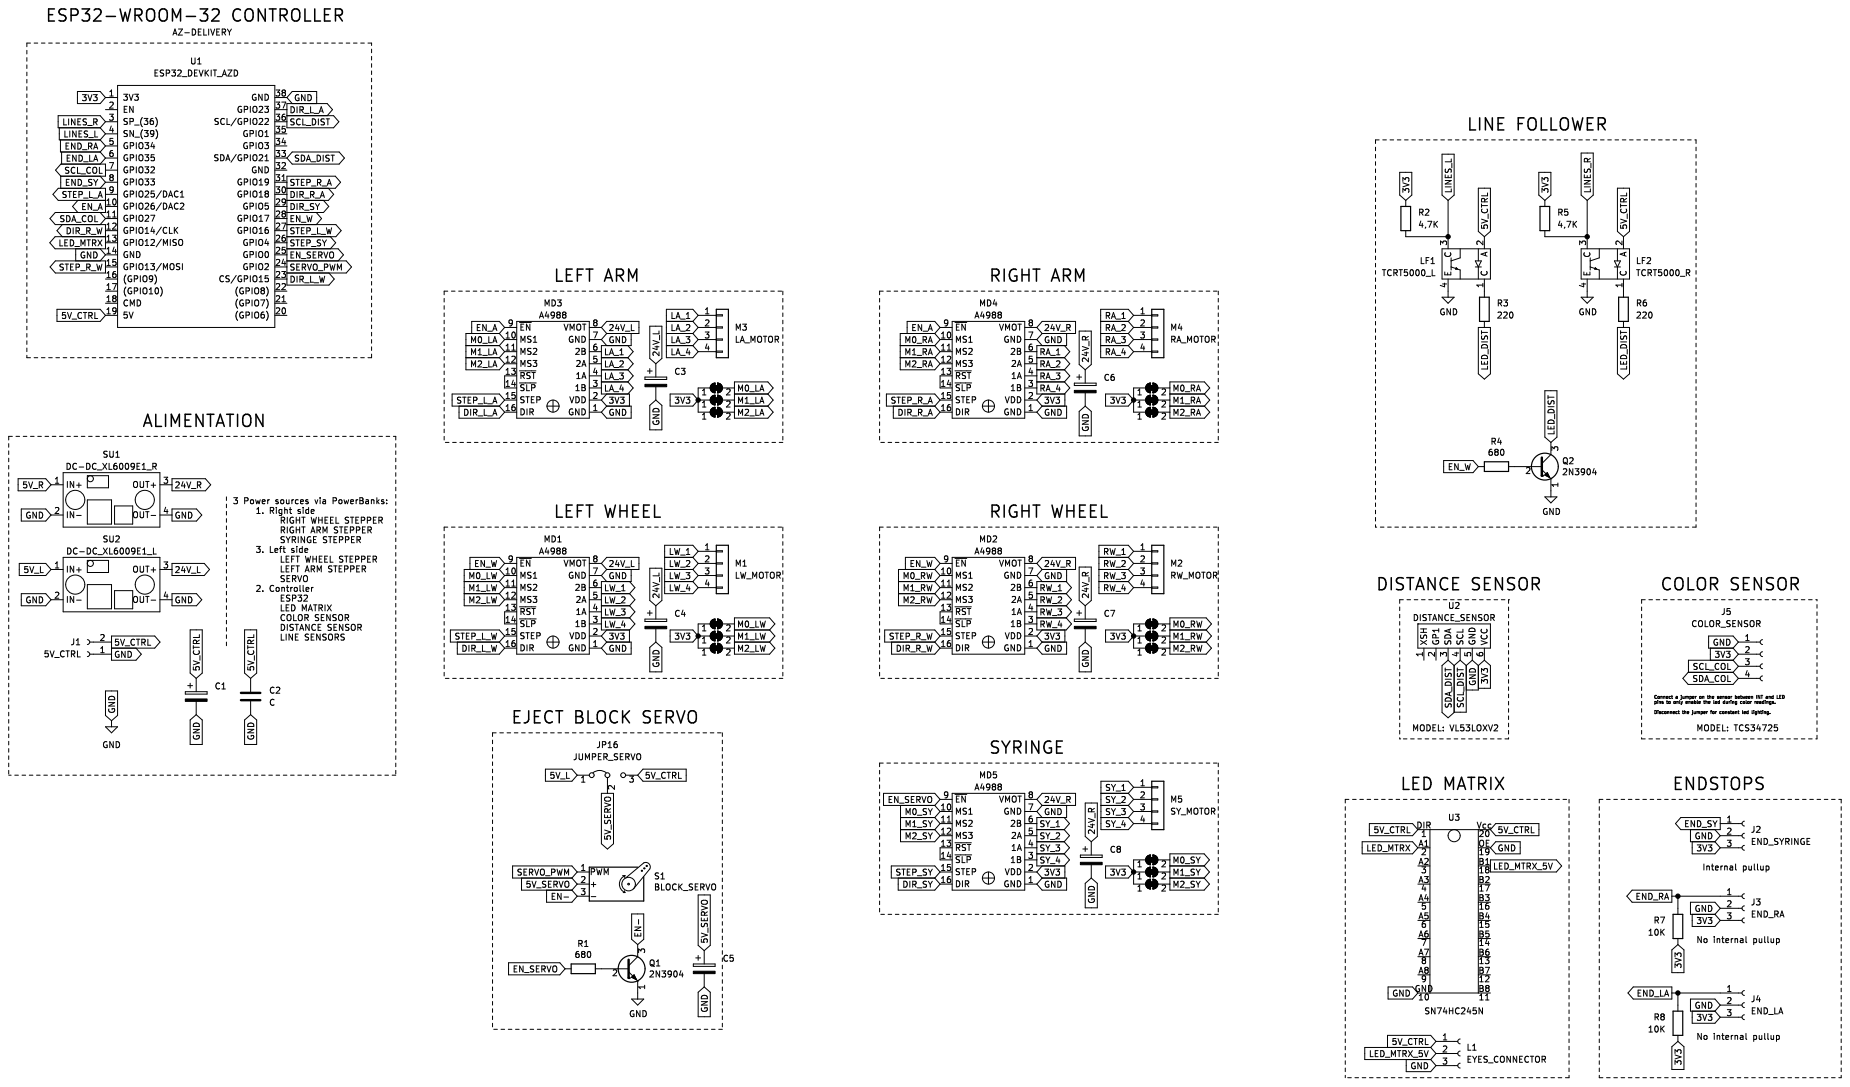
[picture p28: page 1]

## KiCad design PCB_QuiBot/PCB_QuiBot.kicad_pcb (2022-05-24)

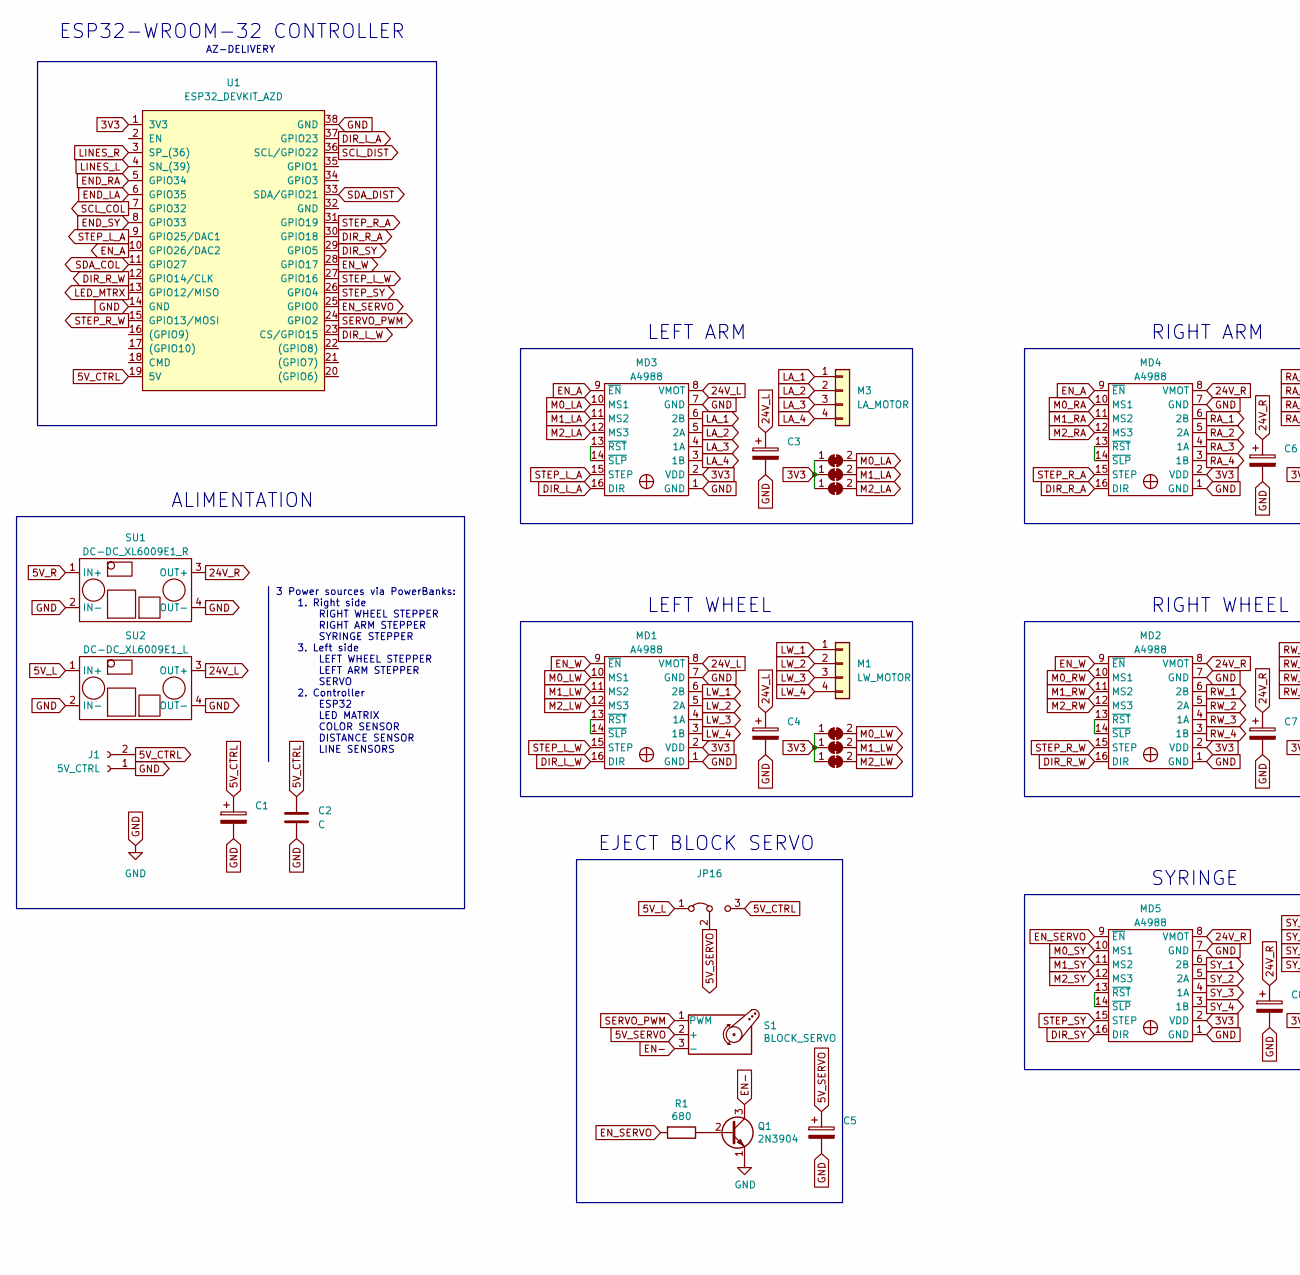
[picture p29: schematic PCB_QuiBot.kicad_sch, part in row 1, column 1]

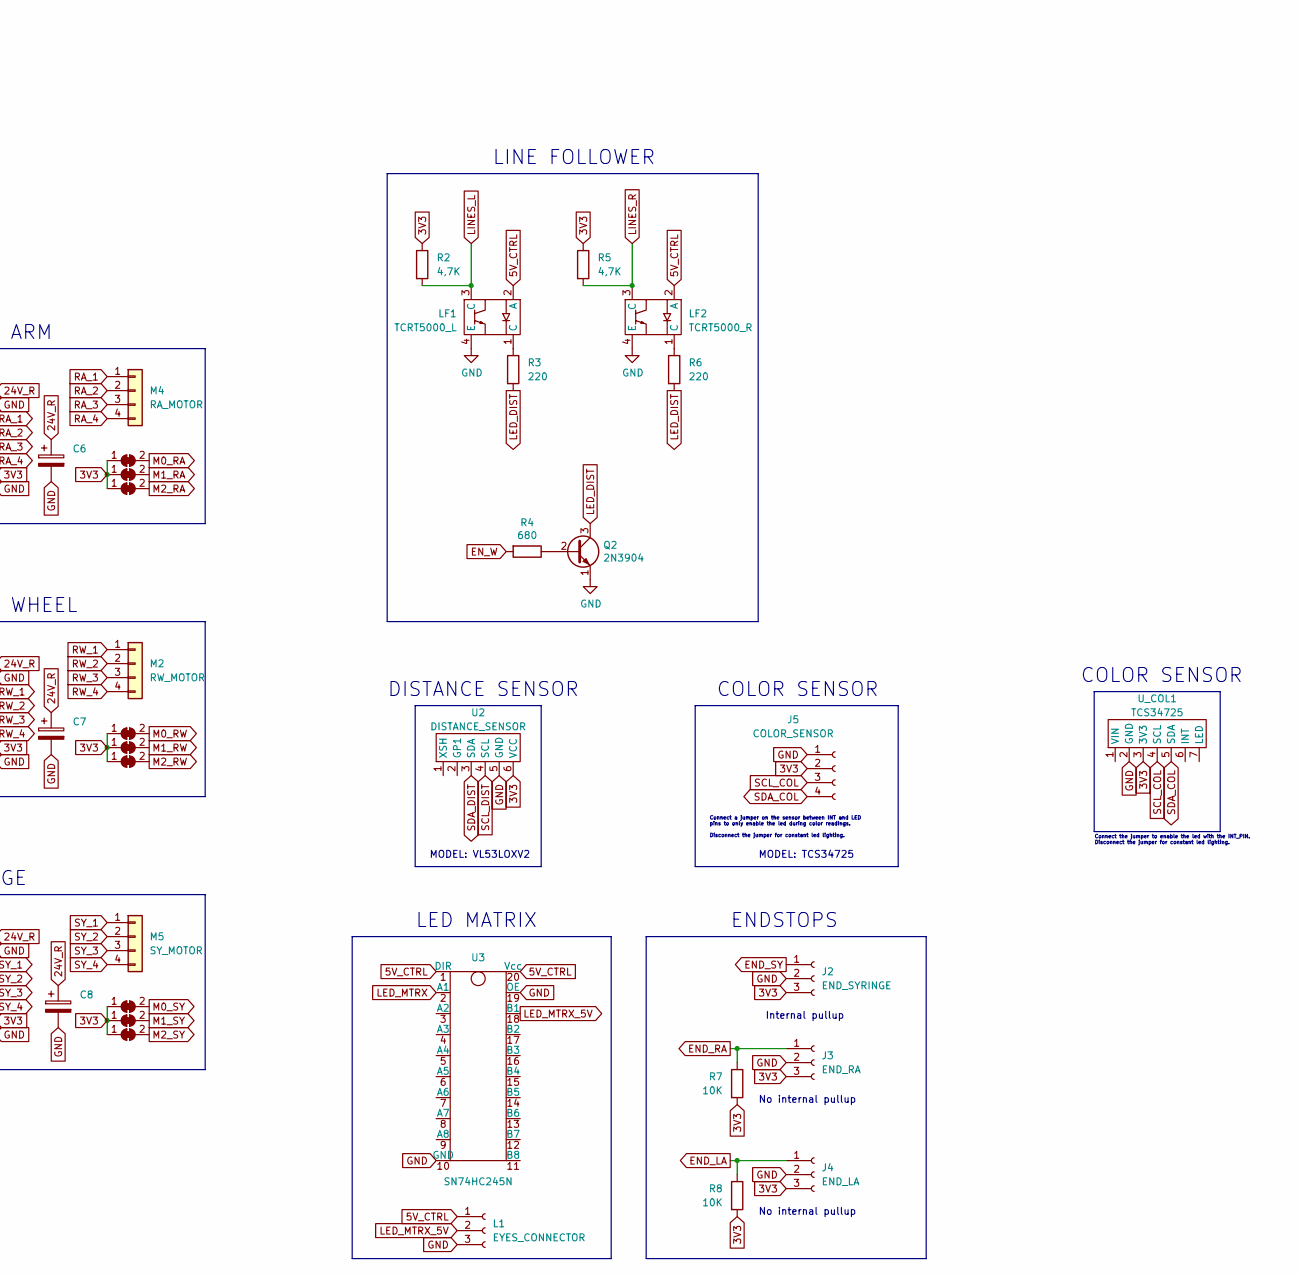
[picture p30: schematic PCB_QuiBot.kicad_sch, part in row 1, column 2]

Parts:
C1: (no value)
C2: C; C_Disc_D4.3mm_W1.9mm_P5.00mm
C3, C4, C5, C6, C7, C8: C_Polarized; CP_Flat_position
J1: 5V_CTRL; PCB_cable_soldering
J2: END_SYRINGE; PinHeader_1x03_P2.54mm_Vertical
J3: END_RA; PinHeader_1x03_P2.54mm_Vertical
J4: END_LA; PinHeader_1x03_P2.54mm_Vertical
J5: COLOR_SENSOR; PinHeader_1x04_P2.54mm_Vertical
JP1, JP2, JP3, JP4, JP5, JP6, JP7, JP8, JP9, JP10, JP11, JP12, JP13, JP14, JP15: SolderJumper_2_Bridged; SolderJumper-2_P1.3mm_Bridged_RoundedPad1.0x1.5mm
JP16: (no value)
L1: EYES_CONNECTOR; PinHeader_1x03_P2.54mm_Vertical
LF1: TCRT5000_L; TCRT5000_Line_follower
LF2: TCRT5000_R; TCRT5000_Line_follower
M1: LW_MOTOR; PinHeader_1x04_P2.54mm_Vertical
M2: RW_MOTOR; PinHeader_1x04_P2.54mm_Vertical
M3: LA_MOTOR; PinHeader_1x04_P2.54mm_Vertical
M4: RA_MOTOR; PinHeader_1x04_P2.54mm_Vertical
M5: SY_MOTOR; PinHeader_1x04_P2.54mm_Vertical
MD1, MD2, MD3, MD4, MD5: A4988; A4988_stepper_driver
Q1, Q2: 2N3904; TO-92_Inline_Wide
R1, R4: 680; R_Axial_DIN0207_L6.3mm_D2.5mm_P10.16mm_Horizontal
R2, R5: 4,7K; R_Axial_DIN0207_L6.3mm_D2.5mm_P10.16mm_Horizontal
R3, R6: 220; R_Axial_DIN0207_L6.3mm_D2.5mm_P10.16mm_Horizontal
R7, R8: 10K; R_Axial_DIN0207_L6.3mm_D2.5mm_P10.16mm_Horizontal
S1: BLOCK_SERVO; PinHeader_1x03_P2.54mm_Vertical
SU1: DC-DC_XL6009E1_R
SU2: DC-DC_XL6009E1_L
U1: ESP32_DEVKIT_AZD; ESP32_DevKit_AZD
U2: DISTANCE_SENSOR; PinHeader_1x06_P2.54mm_Vertical
U3: SN74HC245N
U_COL1: TCS34725

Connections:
3V3: J2.3, J3.3, J4.3, J5.2, JP1.1 (A), JP2.1 (A), JP3.1 (A), JP4.1 (A), JP5.1 (A), JP6.1 (A), JP7.1 (A), JP8.1 (A), JP9.1 (A), JP10.1 (A), JP11.1 (A), JP12.1 (A), JP13.1 (A), JP14.1 (A), JP15.1 (A), MD1.2 (VDD), MD2.2 (VDD), MD3.2 (VDD), MD4.2 (VDD), MD5.2 (VDD), R2.1, R5.1, R7.2, R8.2, U1.1 (3V3), U2.6 (VCC), U_COL1.3 (3V3)
5V_CTRL: C1.1, C2.1, J1.2, JP16.3 (B), L1.1, LF1.2 (A), LF2.2 (A), U1.19 (5V), U3.1 (DIR), U3.20 (Vcc)
5V_L: JP16.1 (A), SU2.1 (IN+)
5V_R: SU1.1 (IN+)
5V_SERVO: C5.1, JP16.2 (C), S1.2 (+)
24V_L: C3.1, C4.1, MD1.8 (VMOT), MD3.8 (VMOT), SU2.3 (OUT+)
24V_R: C6.1, C7.1, C8.1, MD2.8 (VMOT), MD4.8 (VMOT), MD5.8 (VMOT), SU1.3 (OUT+)
DIR_L_A: MD3.16 (DIR), U1.37 (GPIO23)
DIR_L_W: MD1.16 (DIR), U1.23 (CS/GPIO15)
DIR_R_A: MD4.16 (DIR), U1.30 (GPIO18)
DIR_R_W: MD2.16 (DIR), U1.12 (GPIO14/CLK)
DIR_SY: MD5.16 (DIR), U1.29 (GPIO5)
EN-: Q1.3 (C), S1.3 (-)
END_LA: J4.1, R8.1, U1.6 (GPIO35)
END_RA: J3.1, R7.1, U1.5 (GPIO34)
END_SY: J2.1, U1.8 (GPIO33)
EN_A: MD3.9 (~EN), MD4.9 (~EN), U1.10 (GPIO26/DAC2)
EN_SERVO: MD5.9 (~EN), R1.2, U1.25 (GPIO0)
EN_W: MD1.9 (~EN), MD2.9 (~EN), R4.2, U1.28 (GPIO17)
GND: C1.2, C2.2, C3.2, C4.2, C5.2, C6.2, C7.2, C8.2, J1.1, J2.2, J3.2, J4.2, J5.1, L1.3, LF1.4 (E), LF2.4 (E), MD1.1 (GND), MD1.7 (GND), MD2.1 (GND), MD2.7 (GND), MD3.1 (GND), MD3.7 (GND), MD4.1 (GND), MD4.7 (GND), MD5.1 (GND), MD5.7 (GND), Q1.1 (E), Q2.1 (E), SU1.2 (IN-), SU1.4 (OUT-), SU2.2 (IN-), SU2.4 (OUT-), U1.14 (GND), U1.38 (GND), U2.5 (GND), U3.10 (GND), U3.19 (OE), U_COL1.2 (GND)
LA_1: M3.1, MD3.6 (2B)
LA_2: M3.2, MD3.5 (2A)
LA_3: M3.3, MD3.4 (1A)
LA_4: M3.4, MD3.3 (1B)
LED_DIST: Q2.3 (C), R3.2, R6.2
LED_MTRX: U1.13 (GPIO12/MISO), U3.2 (A1)
LED_MTRX_5V: L1.2, U3.18 (B1)
LINES_L: LF1.3 (C), R2.2, U1.4 (SN_(39))
LINES_R: LF2.3 (C), R5.2, U1.3 (SP_(36))
LW_1: M1.1, MD1.6 (2B)
LW_2: M1.2, MD1.5 (2A)
LW_3: M1.3, MD1.4 (1A)
LW_4: M1.4, MD1.3 (1B)
M0_LA: JP1.2 (B), MD3.10 (MS1)
M0_LW: JP4.2 (B), MD1.10 (MS1)
M0_RA: JP7.2 (B), MD4.10 (MS1)
M0_RW: JP10.2 (B), MD2.10 (MS1)
M0_SY: JP13.2 (B), MD5.10 (MS1)
M1_LA: JP2.2 (B), MD3.11 (MS2)
M1_LW: JP5.2 (B), MD1.11 (MS2)
M1_RA: JP8.2 (B), MD4.11 (MS2)
M1_RW: JP11.2 (B), MD2.11 (MS2)
M1_SY: JP14.2 (B), MD5.11 (MS2)
M2_LA: JP3.2 (B), MD3.12 (MS3)
M2_LW: JP6.2 (B), MD1.12 (MS3)
M2_RA: JP9.2 (B), MD4.12 (MS3)
M2_RW: JP12.2 (B), MD2.12 (MS3)
M2_SY: JP15.2 (B), MD5.12 (MS3)
unnamed: LF1.1 (C), R3.1
unnamed: LF2.1 (C), R6.1
unnamed: MD1.13 (~RST), MD1.14 (~SLP)
unnamed: MD2.13 (~RST), MD2.14 (~SLP)
unnamed: MD3.13 (~RST), MD3.14 (~SLP)
unnamed: MD4.13 (~RST), MD4.14 (~SLP)
unnamed: MD5.13 (~RST), MD5.14 (~SLP)
unnamed: Q1.2 (B), R1.1
unnamed: Q2.2 (B), R4.1
RA_1: M4.1, MD4.6 (2B)
RA_2: M4.2, MD4.5 (2A)
RA_3: M4.3, MD4.4 (1A)
RA_4: M4.4, MD4.3 (1B)
RW_1: M2.1, MD2.6 (2B)
RW_2: M2.2, MD2.5 (2A)
RW_3: M2.3, MD2.4 (1A)
RW_4: M2.4, MD2.3 (1B)
SCL_COL: J5.3, U1.7 (GPIO32), U_COL1.4 (SCL)
SCL_DIST: U1.36 (SCL/GPIO22), U2.4 (SCL)
SDA_COL: J5.4, U1.11 (GPIO27), U_COL1.5 (SDA)
SDA_DIST: U1.33 (SDA/GPIO21), U2.3 (SDA)
SERVO_PWM: S1.1 (PWM), U1.24 (GPIO2)
STEP_L_A: MD3.15 (STEP), U1.9 (GPIO25/DAC1)
STEP_L_W: MD1.15 (STEP), U1.27 (GPIO16)
STEP_R_A: MD4.15 (STEP), U1.31 (GPIO19)
STEP_R_W: MD2.15 (STEP), U1.15 (GPIO13/MOSI)
STEP_SY: MD5.15 (STEP), U1.26 (GPIO4)
SY_1: M5.1, MD5.6 (2B)
SY_2: M5.2, MD5.5 (2A)
SY_3: M5.3, MD5.4 (1A)
SY_4: M5.4, MD5.3 (1B)

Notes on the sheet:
No internal pullup
ALIMENTATION
MODEL: VL53LOXV2
RIGHT WHEEL
MODEL: TCS34725
COLOR SENSOR
EJECT BLOCK SERVO
ENDSTOPS
LEFT ARM
ESP32-WROOM-32 CONTROLLER
AZ-DELIVERY
SYRINGE
LINE FOLLOWER
Connect a jumper on the sensor between INT and LED pins to only enable the led during color readings. Disconnect the jumper for constant led lighting.
LEFT WHEEL
DISTANCE SENSOR
LED MATRIX
3 Power sources via PowerBanks: 1. Right side RIGHT WHEEL STEPPER RIGHT ARM STEPPER SYRINGE STEPPER 3. Left side LEFT WHEEL STEPPER LEFT ARM STEPPER SERVO 2. Controller ESP32 LED MATRIX COLOR SENSOR DISTANCE SENSOR LINE SENSORS
Internal pullup
Connect the jumper to enable the led with the INT_PIN. Disconnect the jumper for constant led lighting.
RIGHT ARM

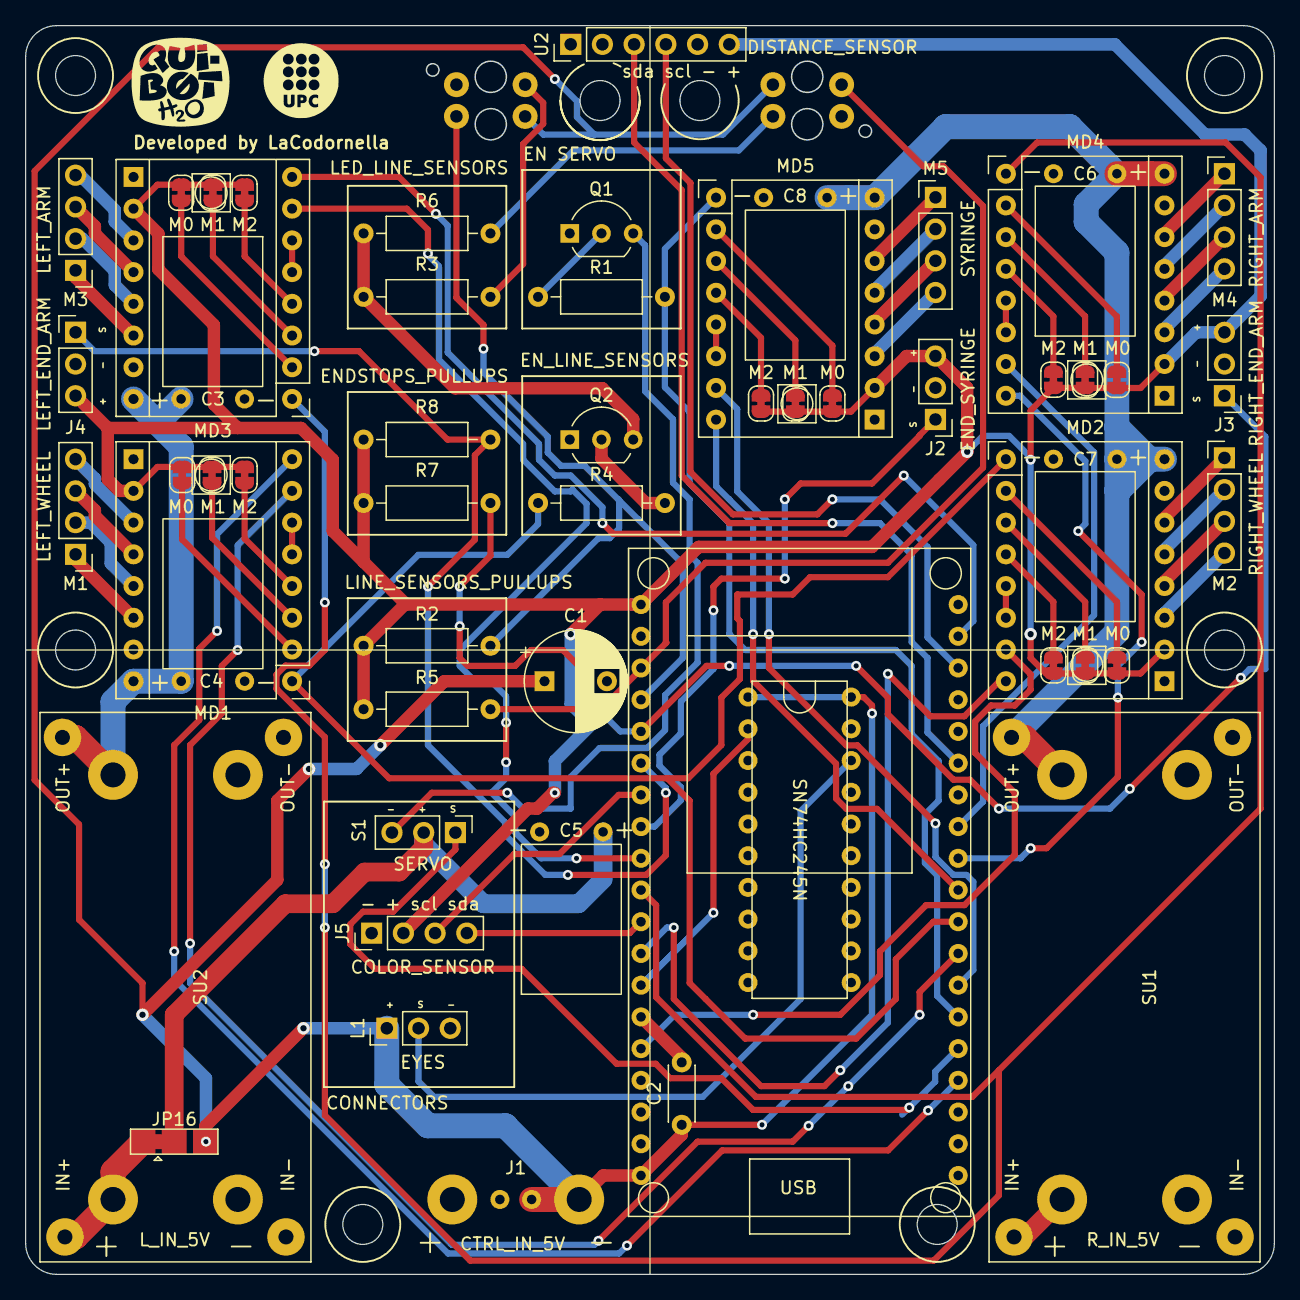
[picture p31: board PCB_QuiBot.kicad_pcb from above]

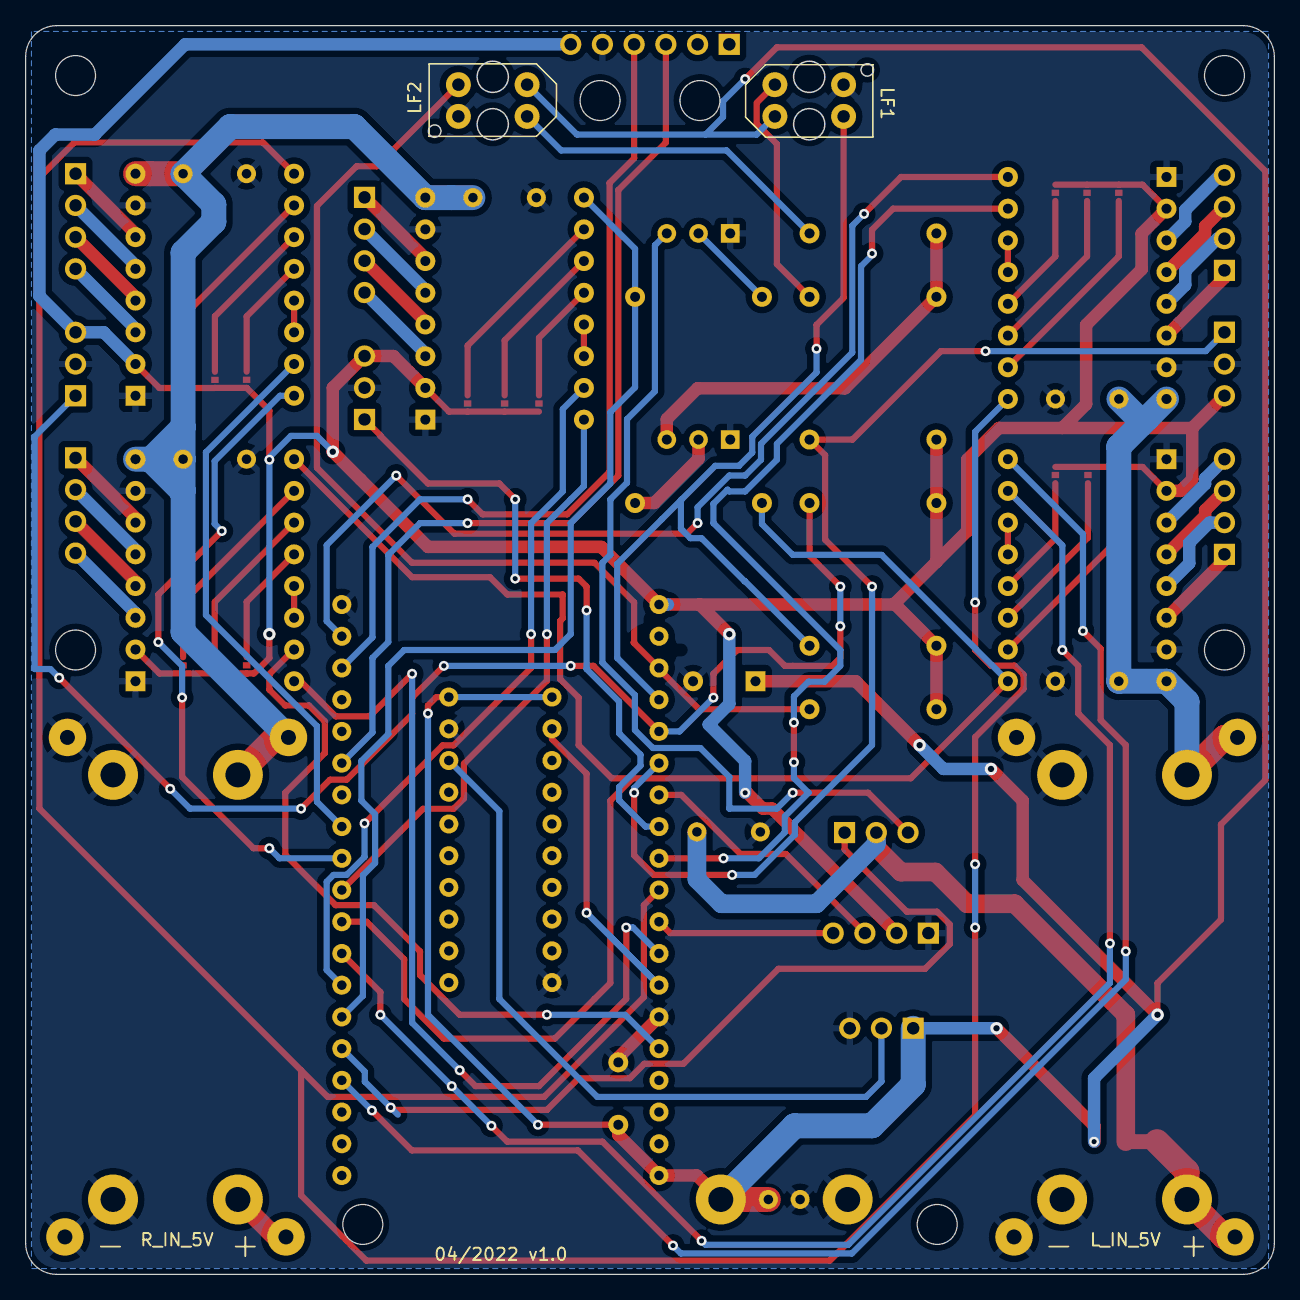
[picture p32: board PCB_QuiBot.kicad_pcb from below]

Board: 2 copper layers, 100.0 x 100.0 mm, 58 parts (2 on the bottom side), 78 nets.

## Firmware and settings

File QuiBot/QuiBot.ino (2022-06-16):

/**
 * @file QuiBot.ino
 * @author Pau Lafoz (pau@lacodornella.cat) & Aleix Badia (aleix@lacodornella.cat)
 * @brief Main Qui-Bot control. Tasks creation and execution
 * @version 0.1
 * @date 2022-05-23
 * 
 */

#include "io.h"
#include "motion.h"
#include "blocks.h"
#include "eyes.h"


TaskHandle_t TaskHandle;
#define CPU_CORE 0
#define APP_CORE 1


/**
 * @brief The following task charges a block, reads its color, executes the required action and waits to finish, and start again.
 * 
 * @param pvParameters Not used.
 */
void task_read_blocks(void *pvParameters){
    (void) pvParameters;

    // Timeouts beetween servo actions
    const uint16_t INSERT_BLOCK_MS  = 2000;
    const uint16_t EJECT_BLOCK_MS   = 2000;
    const uint16_t CHECK_COLOR_MS   = 1000;

    // Got the expected target information to send to `task_move_to`
    static line_follower_response_t expected_target;

    while(true){
        uint8_t color_id;
        bool eyes_state = false;

        eyes_turn_on(&EYES_OPEN, CRGB::Gray);

        // Insert block
        servo_move_to(OPEN_POSITION);

        // Wait until the block is in place
        vTaskDelay(pdMS_TO_TICKS(INSERT_BLOCK_MS));
        
        // Check the block color recursively
        while(true){
            if (distance_to_object() < 80) {
                // Stop block in front of the robot
                if (!eyes_state){
                    eyes_turn_on(&EYES_DOWN, CRGB::Gray);
                    eyes_state = true;
                };
            } else {
                color_id = read_block_color();

                if (eyes_state){
                    eyes_turn_on(&EYES_OPEN, CRGB::Gray, 1, false);
                    eyes_state = false;
                }

                // A color is detected.
                if (color_id != BK) break;

            }
            vTaskDelay(pdMS_TO_TICKS(CHECK_COLOR_MS));
        }

        switch (color_id) {
            case RD:
                /* Red - Go ahead */
                expected_target = CROSSING;
                eyes_turn_on(&EYES_FW, CRGB::DarkRed, 2);
                vTaskDelay(pdMS_TO_TICKS(1000));
                xTaskCreatePinnedToCore(task_move_to, MOVE_TO_CROSSING, 2048, (void*) &expected_target, 1, &TaskHandle, APP_CORE);
                Serial.println(MOVE_TO_CROSSING);
                break;
            
            case GN:
                /* Green - Turn Right */
                eyes_turn_on(&EYES_OPEN, CRGB::DarkGreen, 2);
                vTaskDelay(pdMS_TO_TICKS(1000));
                xTaskCreatePinnedToCore(task_rotate, TURN_90_CW, 1024, (void*) &CW, 1, &TaskHandle, APP_CORE);
                Serial.println(TURN_90_CW);
                break;
            
            case BU:
                /* Blue - Turn Left */
                eyes_turn_on(&EYES_OPEN, CRGB::DarkBlue, 2);
                vTaskDelay(pdMS_TO_TICKS(1000));
                xTaskCreatePinnedToCore(task_rotate, TURN_90_CCW, 1024, (void*) &CCW, 1, &TaskHandle, APP_CORE);
                Serial.println(TURN_90_CCW);
                break;
            
            case YE:
                /* Yellow - Take something */
                eyes_turn_on(&EYES_OPEN, CRGB::Yellow, 2);
                vTaskDelay(pdMS_TO_TICKS(1000));
                xTaskCreatePinnedToCore(task_take_or_leave_something, TAKE_SOMETHING, 2048, (void*) &TAKE, 1, &TaskHandle, APP_CORE);
                Serial.println(TAKE_SOMETHING);
                break;
            
            case OG:
                /* Orange - Leave something */
                eyes_turn_on(&EYES_OPEN, CRGB::OrangeRed, 2);
                vTaskDelay(pdMS_TO_TICKS(1000));
                xTaskCreatePinnedToCore(task_take_or_leave_something, LEAVE_SOMETHING, 2048, (void*) &LEAVE, 1, &TaskHandle, APP_CORE);
                Serial.println(LEAVE_SOMETHING);
                break;
            
            case VT:
                /* Violet - No action */
            //     eyes_turn_on(&EYES_OPEN, CRGB::Purple);
                xTaskCreatePinnedToCore(task_idle, DO_NOTHING, 700, NULL, 1, &TaskHandle, APP_CORE);
                break;
        
            default:
                break;
        }

        while(eTaskGetState(TaskHandle) != eSuspended){
            vTaskDelay(pdMS_TO_TICKS(500));
        }
        
        eyes_turn_on(&EYES_OPEN, CRGB::Gray);

        // Delete task
        vTaskDelete(TaskHandle);


        // Eject block
        servo_move_to(EJECT_POSITION);

        // Wait the block to fall
        vTaskDelay(pdMS_TO_TICKS(EJECT_BLOCK_MS));
    }
}


/**
 * @brief The following functions will be executed once after booting.
 */
void setup(){
    Serial.begin(9600);
    blocks_setup();
    motion_setup();
    eyes_setup();

    arms_home();
    syringe_home();

    xTaskCreatePinnedToCore(task_update_leds, "Update leds", 1024, NULL, 2, NULL, APP_CORE);
    xTaskCreatePinnedToCore(task_read_blocks, "Read Blocks", 2048, NULL, 2, NULL, APP_CORE);
    xTaskCreatePinnedToCore(task_update_steppers, "Update Steppers", 1024, NULL, 1, NULL, APP_CORE);
}


/**
 * @brief Loop is not used, as tasks are already created.
 * 
 */
void loop(){
   vTaskDelay(pdMS_TO_TICKS(1000));
}

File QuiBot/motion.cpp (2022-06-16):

/**
 * @file motion.cpp
 * @author Pau Lafoz (pau@lacodornella.cat) & Aleix Badia (aleix@lacodornella.cat)
 * @brief Controls the wheels, arms and syringe stepper motors from Qui-Bot
 * @version 0.1
 * @date 2022-04-29
 * 
 */

#include "io.h"
#include <AccelStepper.h>
#include <Wire.h>
#include "Adafruit_VL53L0X.h"
#include "motion.h"

// Wheels AccelStepper objects
AccelStepper wheel_R(AccelStepper::DRIVER, STEP_R_W, DIR_R_W);
AccelStepper wheel_L(AccelStepper::DRIVER, STEP_L_W, DIR_L_W);

// Arms AccelStepper objects
AccelStepper arm_R(AccelStepper::DRIVER, STEP_R_A, DIR_R_A);
AccelStepper arm_L(AccelStepper::DRIVER, STEP_L_A, DIR_L_A);

// Syringe AccelStepper object
AccelStepper syringe(AccelStepper::DRIVER, STEP_SYRINGE, DIR_SYRINGE);

// Distance sensor object
Adafruit_VL53L0X dist_sensor = Adafruit_VL53L0X();

// Task name strings
const char* MOVE_TO_CROSSING    = "Move to crossing";
const char* TURN_90_CW          = "Turn 90 CW";
const char* TURN_90_CCW         = "Turn 90 CCW";
const char* MOVE_TO_OBJECT      = "Move to object";
const char* TAKE_SOMETHING      = "Take something";
const char* LEAVE_SOMETHING     = "Leave something";
const char* DO_NOTHING          = "Do nothing";

/*****************
 * Motion Params *
 *****************/
float wheels_max_speed  = 130;      // The desired maximum speed in steps per second
float wheels_accel      = 190;      // The desired acceleration in steps per second per second
float arms_max_speed    = 250;      // The desired maximum speed in steps per second
float arms_accel        = 125;      // The desired acceleration in steps per second per second
float syringe_max_speed = 800;      // The desired maximum speed in steps per second
float syringe_accel     = 500;      // The desired acceleration in steps per second per second

// Wheels
const uint8_t WHEEL_MECH_REDUCTION          = 5;
const uint16_t WHEEL_STEPS_PER_REVOLUTION   = 200 * WHEEL_MECH_REDUCTION;
const uint8_t MM_TO_CROSSING_CENTER         = 62;
const uint8_t MM_TO_OBJECT                  = 20;
const uint16_t BLACK_THRESHOLD              = 1500;          // Value to be considered black.


// Arm positions
const uint16_t ARM_LOWER_POSITION     = 120;  // Steps from home to lower position
const uint16_t ARM_L_UPPER_POSITION   = 900;  // Steps from home to upper position
const uint16_t ARM_R_UPPER_POSITION   = 550;  // Steps from home to upper position

// True when the wheels are controlled by speed target, false when position target.
bool wheels_speed_mode              = false;

// Frequency in Hz to check the line follower
const uint8_t LINE_FOLLOWER_FREQ    = 100;  

// Period in ms to check the line follower
const uint8_t LINE_FOLLOWER_PERIOD  = 1000 / LINE_FOLLOWER_FREQ;

/**
 * @brief Enables or disables the wheel steppers 
 * 
 * @param state `ON` or `OFF`
 */
void enable_wheels(bool state){
    digitalWrite(EN_W, state);
}


/**
 * @brief Enables or disables the arm steppers 
 * 
 * @param state `ON` or `OFF`
 */
void enable_arms(bool state){
    digitalWrite(EN_A, state);
}


/**
 * @brief Enables or disables the syringe stepper 
 * 
 * @param state `ON` or `OFF`
 */
void enable_syringe(bool state){
    digitalWrite(EN_SERVO, state);
}


/**
 * @brief Returns `true` when the hall effect endstop is detecting.
 * 
 * @param pin where the endstop is connected.
 */
bool is_endstop_detecting(uint8_t pin) {
    return !digitalRead(pin);
}


/**
 * @brief Move both arms to a position in steps from home and wait to arrive. The task calls `vTaskDelay()` to allow other tasks run.
 * 
 * @param int16_t position in steps from home
 */
void move_arms_to(int16_t position) {
    arm_L.moveTo(position);
    arm_R.moveTo(position);

    while (arm_L.distanceToGo() != 0 && arm_R.distanceToGo() != 0) {
        vTaskDelay(pdMS_TO_TICKS(100));
    }
}

void move_arms_up() {
    arm_L.moveTo(ARM_L_UPPER_POSITION);
    arm_R.moveTo(ARM_R_UPPER_POSITION);

    while (arm_L.distanceToGo() != 0 && arm_R.distanceToGo() != 0) {
        vTaskDelay(pdMS_TO_TICKS(100));
    }
}


/**
 * @brief Move both wheels to a position in steps from home and wait to arrive. The task calls `vTaskDelay()` to allow other tasks run.
 * 
 * @param int16_t position in steps from home
 * @param bool invert one of the wheels to make the robot turn (optional, false by default)
 */
void move_wheels_to(int16_t position, bool invert = false) {
    wheel_L.moveTo(position);
    wheel_R.moveTo(invert ? -position : position);

    while (wheel_L.isRunning() && wheel_R.isRunning()) {
        vTaskDelay(pdMS_TO_TICKS(100));
    }
}

void wheels_set_position(long position = 0){
    wheel_L.setCurrentPosition(position);
    wheel_R.setCurrentPosition(position);
}

void wheels_set_speed(float speed, bool rotate = false, bool dir = CW){
    if (rotate) {
        wheel_L.setSpeed(dir == CW ? speed : -speed);            
        wheel_R.setSpeed(dir == CW ? -speed : speed);            
    } else {
        wheel_L.setSpeed(speed);
        wheel_R.setSpeed(speed);
    }
}

/**
 * @brief Steppers setup (acceleration, max speed...) and distance sensor
 */
void motion_setup(){
    // Enable pins
    pinMode(EN_W, OUTPUT);
    pinMode(EN_A, OUTPUT);
    pinMode(EN_SERVO, OUTPUT);
    pinMode(END_L_A, INPUT);
    pinMode(END_R_A, INPUT);
    pinMode(END_SYRINGE, INPUT);

    enable_arms(OFF);
    enable_wheels(OFF);

    // Stepper parameters
    wheel_R.setMaxSpeed(wheels_max_speed);
    wheel_R.setAcceleration(wheels_accel);
    wheel_L.setMaxSpeed(wheels_max_speed);
    wheel_L.setAcceleration(wheels_accel);
    arm_R.setMaxSpeed(arms_max_speed);
    arm_L.setMaxSpeed(arms_max_speed);
    arm_R.setAcceleration(arms_accel);
    arm_L.setAcceleration(arms_accel);
    syringe.setMaxSpeed(syringe_max_speed);
    syringe.setAcceleration(syringe_accel);

    // Distance sensor init
    Wire.begin();
    if (!dist_sensor.begin(0x31, true, &Wire)) {
        Serial.println("Could not find VL53LOX laser distance sensor!");
    } else {
        Serial.println("VL53LOX Laser distance sensor connected.");
    }
}


uint32_t mm_to_steps(uint16_t mm) {
    // Perímetre roda Ø152mm = 2 * PI * 76 = 477.28mm
    // Voltes totals per 1mm = 1 / 477.28 = 0.002 voltes de roda
    return ((mm * WHEEL_STEPS_PER_REVOLUTION * 2) / 1000);
}

/*****************
 * HOMING CYCLES *
 *****************/
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

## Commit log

2022-05-23 First working QuiBot prototype
2022-05-24 Added Kicad project
    [PCB_QuiBot.kicad_pcb, PCB_QuiBot.kicad_sch, PCB_QuiBot.step]
2022-05-24 Added PCB images, pdf schematic and readme
2022-05-30 Docs added
    [Arms_motors_support_bottom.STL, Arms_motors_support_top.STL, Ball_support.STL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]
2022-05-30 Assembly process added
2022-05-30 BOM added
    [BOM.ods]
2022-05-30 BOM on readme
2022-05-30 3D parts list added
    [3D_Parts_list.ods]
2022-05-30 Printing considerations
2022-05-30 Arduino program readme
2022-06-02 FDM printer
2022-06-14 Motion changes. Wheels always in speed mode.
